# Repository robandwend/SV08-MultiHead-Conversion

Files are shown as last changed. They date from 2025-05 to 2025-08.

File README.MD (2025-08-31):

# SOVOL SV08 Multihead Conversion

I've converted my SV08 to a multi-toolhead printer. I'm keeping the costs way down by using the standard SV08 toolheads.

This repo contains the files designs I've used for mounting on the SV08.

NOTE: Files may change as I continue to develop this project - please refer to the commit's to see what's changed.

For full build overview on a SV08, I suggest watching Teaching Tech's series on doing the conversion. At this time he's not yet finished, and hasn't published any of the cad work - hence me re-inventing the wheel in this design. 
[video link](https://www.youtube.com/watch?v=G6kc_BnYU8w&t=2s)

For an initial intro here's a quick video I did to show the mount. 
[video link](https://www.youtube.com/watch?v=clDU7j5NY64)

## ModularDock

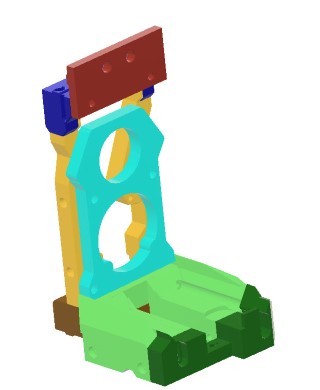
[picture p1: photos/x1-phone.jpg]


The head mount is based on using the modulardock From 
[here](https://github.com/DraftShift/ModularDock)

Specifically using these Components
- FrameShort
- 2020

The rear components for the SV08 modular dock can be found in the stl's folder.

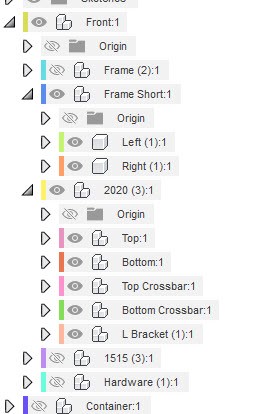
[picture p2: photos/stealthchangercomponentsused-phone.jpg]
Components


## *NEW* Modular dock - improved rest

I has now added a 2nd version of the dock components, implementing a better nozzle rest using a 5972k91 bearing (most common bearing used in many projects). This has been added to reduce nozzle 'dribble' whilst mounted. Two cut-down pen-springs are used to float the bearing.

The backplane stl is not needed with this version, as it's incorporated into the base itself.

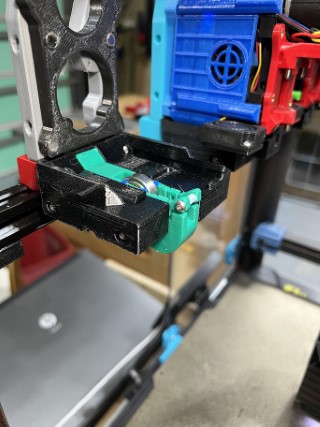
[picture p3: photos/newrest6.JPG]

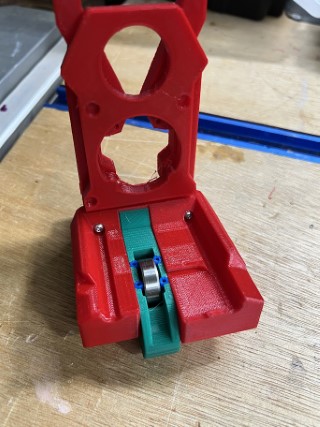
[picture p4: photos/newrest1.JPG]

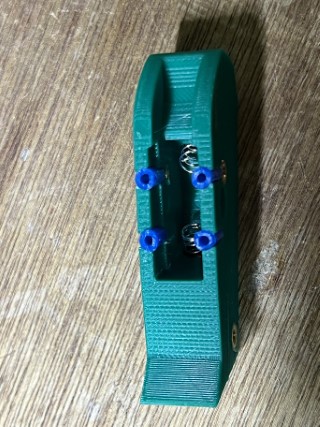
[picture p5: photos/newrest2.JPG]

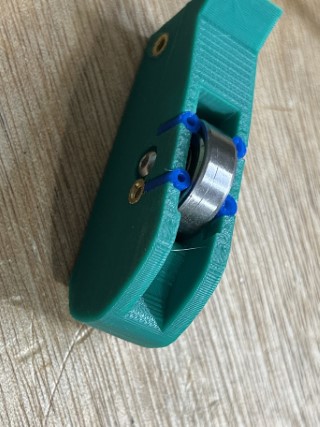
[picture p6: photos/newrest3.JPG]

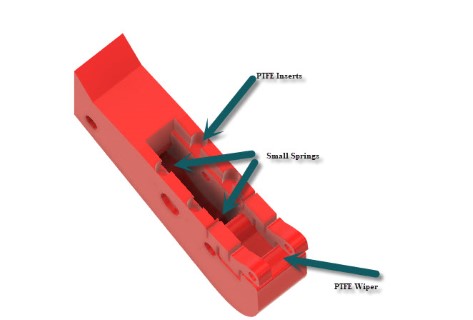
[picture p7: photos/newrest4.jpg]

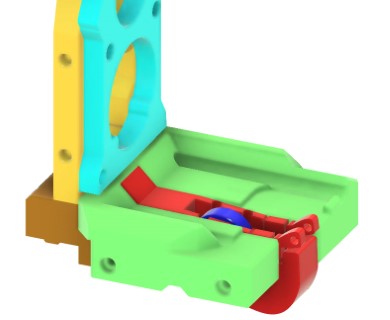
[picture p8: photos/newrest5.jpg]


## Stealthchanger 

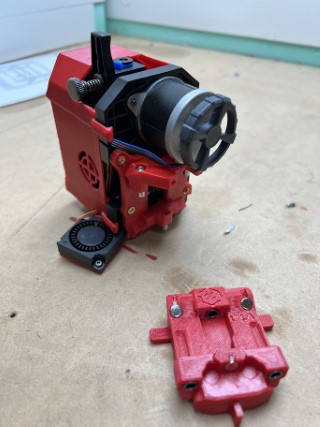
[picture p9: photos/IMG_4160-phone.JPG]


Follow the stealthchanger information found here - 
[link](https://github.com/DraftShift/StealthChanger)

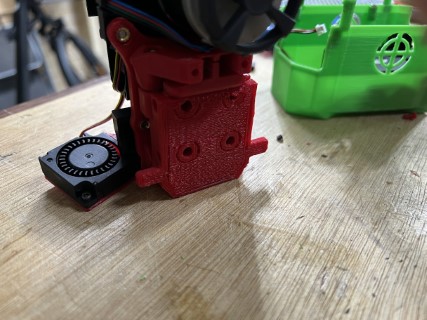
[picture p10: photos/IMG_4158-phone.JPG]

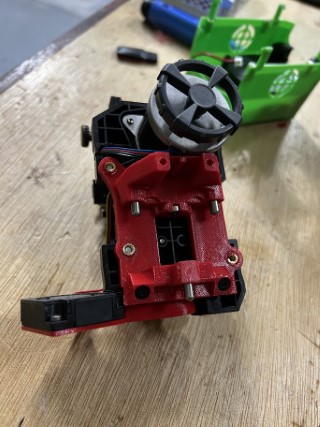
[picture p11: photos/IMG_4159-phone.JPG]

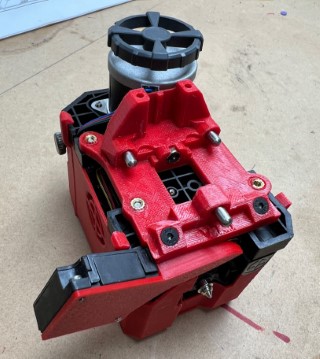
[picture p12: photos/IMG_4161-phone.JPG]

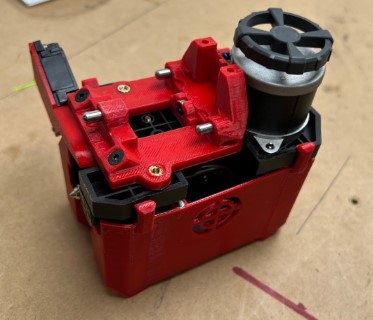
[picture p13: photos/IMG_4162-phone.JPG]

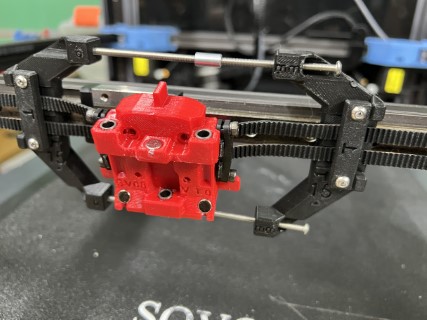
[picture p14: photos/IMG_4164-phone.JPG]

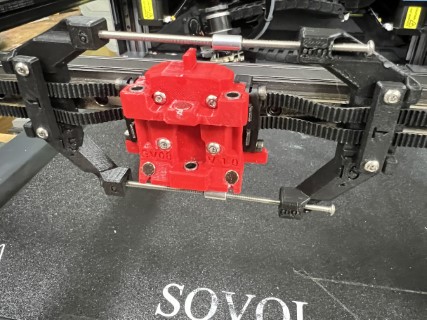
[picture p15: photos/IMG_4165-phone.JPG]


## Supports for docks

### Top 2020

The top 2020 extrusion has pre-built supports. Due to it's lenght and the small bolt holes, please ensure you compensate for any shrinkage when printing - size accuracy is key.

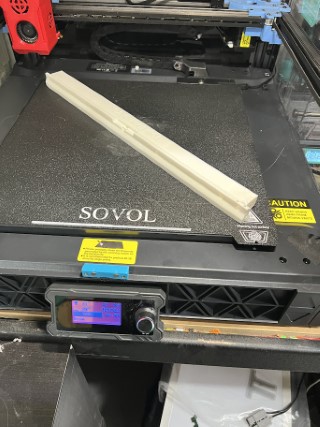
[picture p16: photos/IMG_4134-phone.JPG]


I've added a wave to the supports to try to assist with warping when printing in ABS/ASA

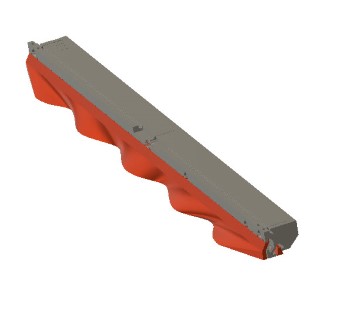
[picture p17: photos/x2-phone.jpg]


The print has supports built in, which will need snapping off after printing...

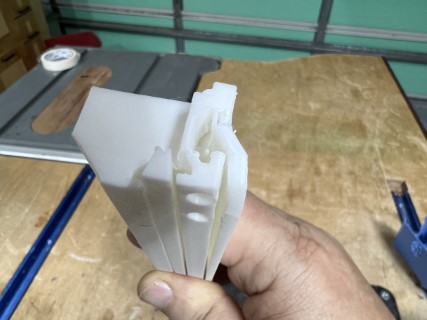
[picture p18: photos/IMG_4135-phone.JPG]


The light will need relocating (the screw holes can be used in attaching the 2020). I used some standard voron type tape to attach as shown.

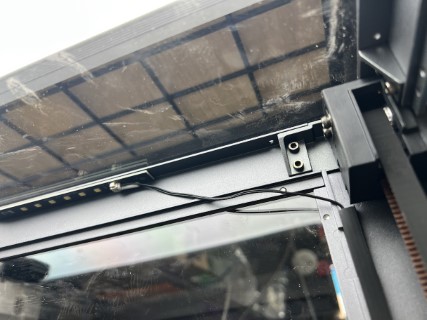
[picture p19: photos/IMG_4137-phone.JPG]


### Lower 2020

The bottom 2020 support pieces also have a hole printing guide. You MUST drill and tap, the bolt must NOT extend into the rear channel, since it would collide with the Z-Axis.

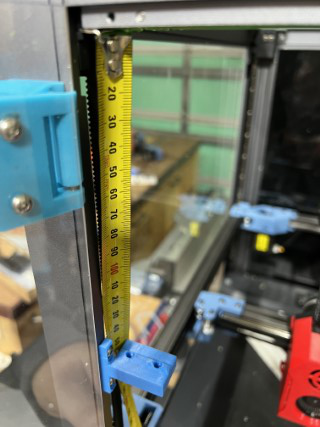
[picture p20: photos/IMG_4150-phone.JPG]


The head cover has built in supports for the clips, but may need manual supports on the front left/right indent area (depending on how well your bridging works.

Magnets - I've replaced the standard 4x3 magnets with 4x6 (or two 4x3) to increase pull strength.

## New power supply

I used this supply 
[supply link](https://www.amazon.com.au/dp/B0CN1JVD4Y?ref=ppx_yo2ov_dt_b_fed_asin_title&th=1)

And these mounts 
[mounts link](https://www.printables.com/model/1047201-sovol-sv08-power-supply-upgrade-mounting-parts)

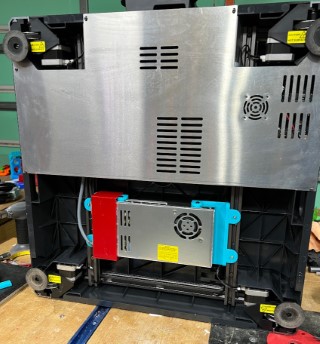
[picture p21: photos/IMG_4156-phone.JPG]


## Wiring General

I followed the method used by Teaching Tech 
[video link](https://youtu.be/OFGBXBn_xqs?t=1077)
using a birds-nest 
[birdsnest link](https://github.com/xbst/Birds-Nest)
 here's a handy clip from Teaching-Tech's video.
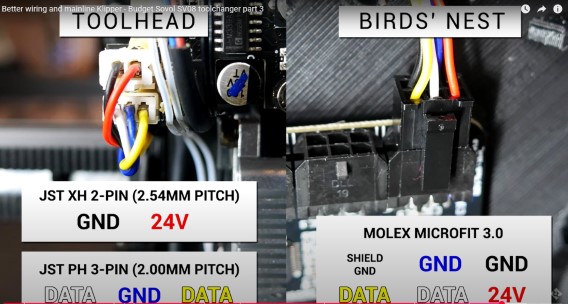
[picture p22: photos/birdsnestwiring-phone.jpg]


There's a simple birdnest attachment for the standard birdsnest fannypack_base that allows insertion of strain wires in the STL folder.
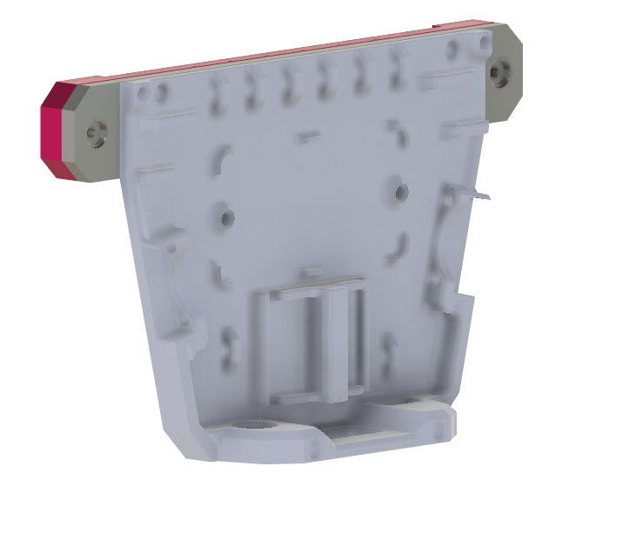
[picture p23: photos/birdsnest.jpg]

I bolted this to the rear of the SV08 - having drilled two small holes to bolt into.

## Rear fan

The rear fan is moved to allow undocking of the head. Simply removed the fan and replace the mount with the new one. 

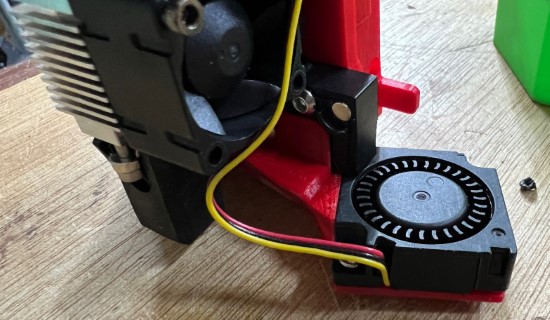
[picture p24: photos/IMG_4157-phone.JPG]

Components
Components
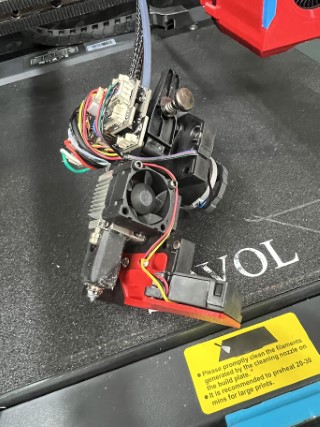
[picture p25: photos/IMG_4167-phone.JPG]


Note that this is fastened in the same holes, but from the front of the back plate rather than the back. 8mm M3 bolts will be needed.
To fasten the fan back on to the mount, either use the original bolts, or I have found using a 5mm M2.5 bolts gives a stronger fitting.

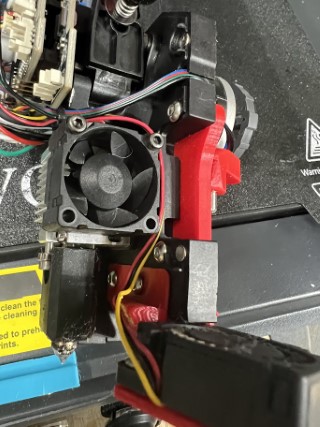
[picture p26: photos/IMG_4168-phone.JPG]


## Head cover

The design relies on this printed replacement head cover, which has additional rear clips, longer magnets, and 3 front magnets which attach to the dock. It also has additional cutouts to allow for the moved rear fan.

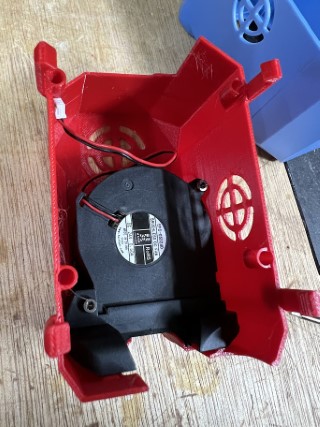
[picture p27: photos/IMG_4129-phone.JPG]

Components

## Umbilical mount point

To ensure the hotend umbilical could be adjusted to avoid collisions. This extension to the standard wire mount adds a small extension into which the strengthening wire could be mounted.

Note: A small recess should be made into the head-cover to fit this mount point. (I'll change the head-cover design at some point).

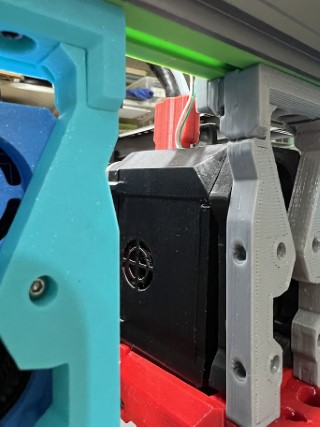
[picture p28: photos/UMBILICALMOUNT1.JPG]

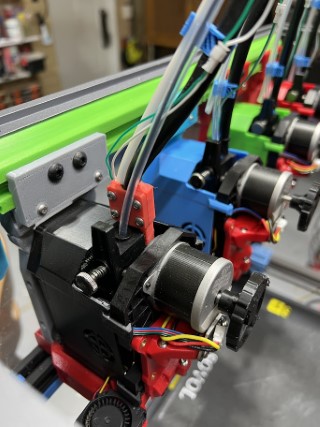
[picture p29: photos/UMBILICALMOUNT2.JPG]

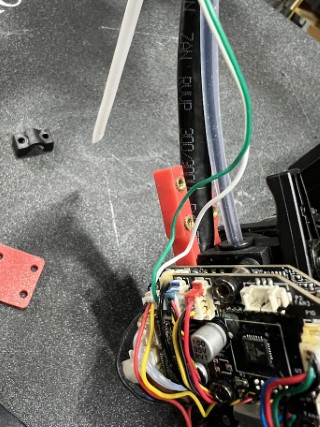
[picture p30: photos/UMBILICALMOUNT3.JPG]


## Bed Raise

The SV08 stealthchanger mount moves the head up 15mm and slightly forward. It will require raising.

The bed shims require M4 thread inserts.

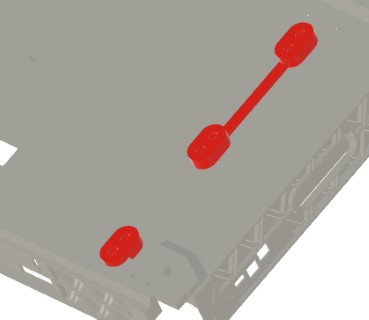
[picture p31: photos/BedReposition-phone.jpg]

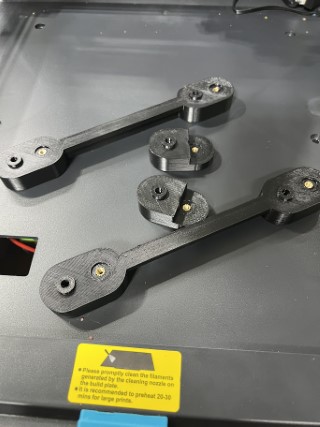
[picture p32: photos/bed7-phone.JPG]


Remove the bed, insert the shims as below (it may be a tight fit) use the 6 original bed screws to fasten the shims. Use 6 new M4 screws to fasten down the bed in it's new position.
Re-wire the bed.

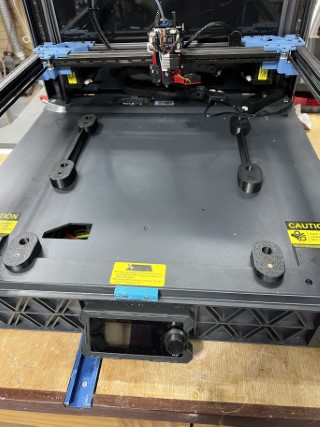
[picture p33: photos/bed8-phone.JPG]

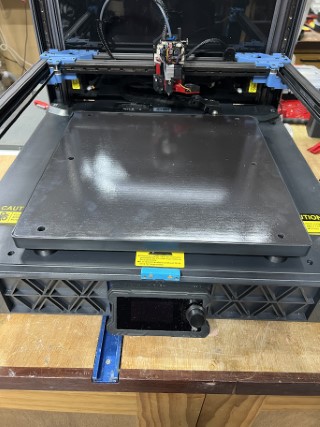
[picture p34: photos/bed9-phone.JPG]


## Sexball / SexBolt

To allow for automated x-y-z calibration between the heads [see this](https://github.com/viesturz/klipper-toolchanger/blob/main/tools_calibrate.md) I'm using a Sexball [sexball](https://github.com/DraftShift/StealthChanger/wiki/Bill-of-Materials#sexball-probe) which is based on the Sexbolt [sexbolt](https://mods.vorondesign.com/details/t1DBVlcUBbdEK6habEsVzg)

I reduced the height of the ball by 4mm to make it closer to the bed, by cutting the bar (with an angle grinder). This isn't required, but I felt it looked better.

NOTE: The use of the sexball requires the bed moving forward an extra 5mm - versions of the shim STL's are marked for this change.

This allows the tools_calibrate macro [macros](https://github.com/viesturz/klipper-toolchanger/blob/main/tools_calibrate.md) to be used to align all the heads.
	
### TOOL ALIGNMENT

I found these instructions to be the easiest way to align.
[tool alignment](https://github.com/viesturz/NozzleAlign) - to get the offsets of the tools from the sexball 

Here's the command sequence I ran:
> T0\
> SET_HEATER_TEMPERATURE HEATER=extruder TARGET=200\
> G28\
> CLEAN_NOZZLE\
> MOVE_OVER_PROBE\
> TOOL_LOCATE_SENSOR     # Sensor location at 281.150000,354.818750,1.853125\
> SET_HEATER_TEMPERATURE HEATER=extruder TARGET=0\

-- At this point I check the location with that defined in calibration-offsets.cfg, if they are off, then correct them and restart.

> SET_HEATER_TEMPERATURE HEATER=extruder1 TARGET=200\
> T1                     # Note my load/unload does an auto CLEAN-NOZZLE each time\
> MOVE_OVER_PROBE\
> TOOL_CALIBRATE_TOOL_OFFSET           # T1 = Tool offset is -0.662500,-0.031250,-0.290625\
> SET_HEATER_TEMPERATURE HEATER=extruder1 TARGET=0\

Repeat the above for T2,3,4

_T1 = Tool offset is -0.662500,-0.031250,-0.290625_\
_T2 = Tool offset is -0.750000,0.300000,0.163125_\
_T3 = Tool offset is -1.106250,-0.531250,-0.165000_\
	
Finally to ensure the belts haven't slipped (eg docking errors) I recheck location of T0...

> SET_HEATER_TEMPERATURE HEATER=extruder TARGET=200\
> T0\
> MOVE_OVER_PROBE\
> TOOL_CALIBRATE_TOOL_OFFSET\
> SET_HEATER_TEMPERATURE HEATER=extruder TARGET=0\

_Final T0 = _Tool offset is -0.000000,-0.006250,0.037500_  :-) Close enough :-)_

## TOPHAT

Based from Nadir's top hat [tophat](https://www.printables.com/model/865851-sovol-sv08-top-hat), I designed a tall version with clear panels and a magnetic rear access cover for the cabling.

Here you see the tophat with all it's parts colour seperated. 

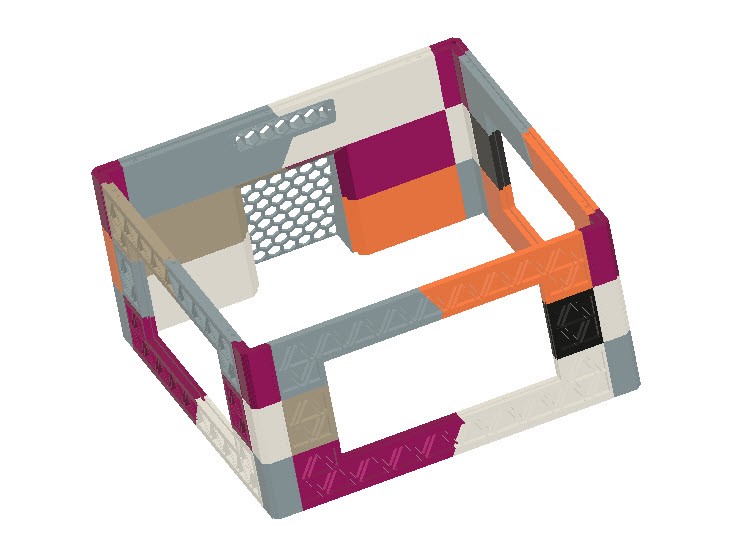
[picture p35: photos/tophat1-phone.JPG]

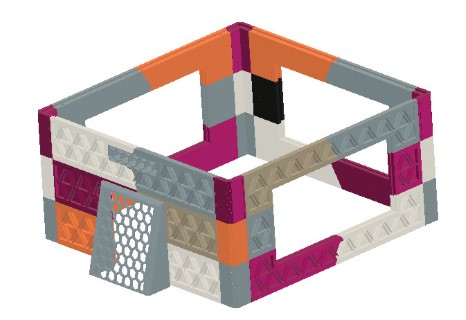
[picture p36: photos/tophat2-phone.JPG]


## RUNOUT DETECTOR

I've added a simple inline runout detector based on [this]https://www.printables.com/model/1084240-sovol-sv08-runout-sensor-on-head 
My version is here [my version]https://www.printables.com/model/1299711-generic-inline-runout-detector

Note it uses a 5.5mm ball (original used 5mm).

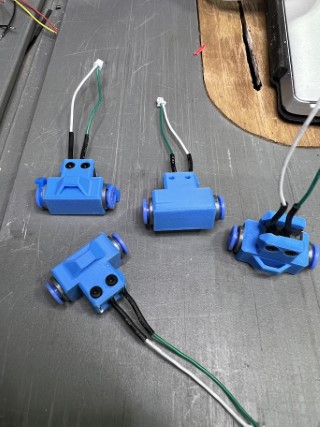
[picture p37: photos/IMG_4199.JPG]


Here you can see the wiring for the DETECTOR

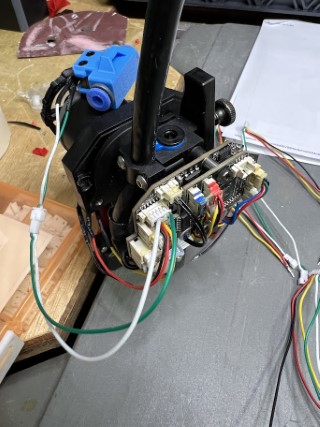
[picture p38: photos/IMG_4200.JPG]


## REAR ROCKER

Here's a simple rocker to allow the SV08 to be moved to it's back without squashing any cables at the rear.

The bottom part can use the original bolts since they appear to have plenty of spare length.

The top two bolts (holding in the panels) need replacing with 8mm m3's

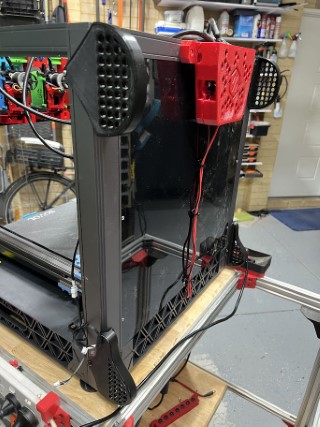
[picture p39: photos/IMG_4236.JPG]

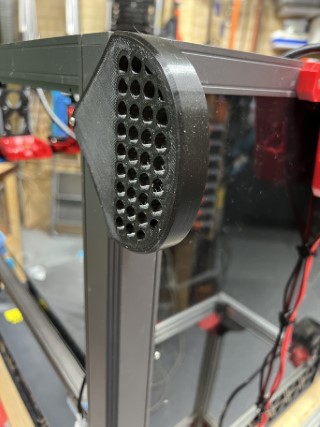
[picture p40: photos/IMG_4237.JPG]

Components

## BASE cover

Here's a simple cover to replace the stock metal one (still using the original fan) - I was not a fan of the original.

This will require a 36mm M3 bolt and an M3 2020 T-nut

Components

## Gantry Mounted wiper

I've created a modified version of [link] (https://www.printables.com/model/882364-new-version-adjustable-gantry-mounted-nozzle-seal) that has an extended and raised arm to fit this SV08 change. This can be seen in use in some of the videos.

## Final Klipper config files

My active klipper config files can all be found [here](https://github.com/robandwend/sv08-klipper)

# Over the top options...

As I've continued to tinker with this printer, I've made a few other modifications just for the fun of It

## Bambulab nozzle replacement.

I've used this converter to convert all nozzles to bambulabs. The original nozzles worked fine, but since all my other printers either use natively or have been converted to bambu nozzles, I thought I'd do this SV08 as well.

I've used both these converters
[link](https://www.printables.com/model/966176-remix-of-stephzics-sovol-sv08-bambu-lab-nozzle-ada)
[link](https://www.printables.com/model/944360-sovol-sv08-bambulab-clone-hotend-support)

Components
Components

## Extra camera processing

I've moved all camera processing (including new ones listed below) to an additional Raspberry PI 4B (I had it spare).
This is  running crowsnest to publish the cameras. The original klipper config for the camera's now points their IP's to this additional processor.

Components

A mount for this PI is in /stls/extras/

## Nozzle Cam

I've used this nozzle cam (only currently on head0)
[link](https://www.mintion.net/products/mintion-nozzle-camera?variant=48352784122166)

STL's for the head mount and electronics box are in /stls/extras/
nozzlecameramount

## Extra Camera's

In addition to the nozzle camera, I've added a camera to the rear top bar of the frame. 

This camera [link](https://www.aliexpress.com/item/1005005249688226.html)

Mount for the camera is in /stls/extras/

## Voice addition

Since I've now for the spare PI installed, I decided to add some speach to the printer.

I've added two small speakers (and a speaker pi-hat I had spare)...

The speakers were simply hot glued in place...

Components
Components
Components

Text to speach is achieved using pipper (see this video 
[link](https://www.youtube.com/watch?v=rjq5eZoWWSo_)
 - although the installation method has changed somewhat since the video was made.
 
 Here's the location of piper [link](https://github.com/OHF-Voice/piper1-gpl)
 
 In short, the install command is
 - pip install piper-tts  --break-system-packages
 
 (Test without the break-system-packages option first, to see if it's required on your installation).
 
 To get my audio amplifier working I had to do the following (thanks chatgpt)...

Edit /boot/config.txt and add the line:

   dtoverlay=audremap,pins_18_19

and reboot

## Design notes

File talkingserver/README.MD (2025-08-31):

# TALKING SERVER

Here's a simple way to add spoken audio to your klipper printer macros.

You'll need a raspberry pi to run the piper text-to-speech module. This could be your printers klipper CPU. This shouldn't affect the CPU load for printing, since usually you'll only need audio prompts when nothing is actually being printed (print starts, and error, print paused, load-more-filament, print-completed etc.).

## Add speakers

Either use the headphone jack of the PI or an audio tophat and some small speakers, and check audio works on the PI 

I've added two small speakers (and a speaker pi-hat I had spare)...

The speakers were simply hot glued in place...

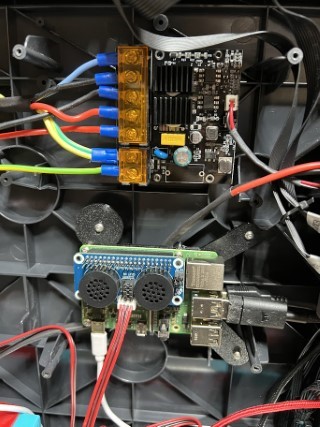
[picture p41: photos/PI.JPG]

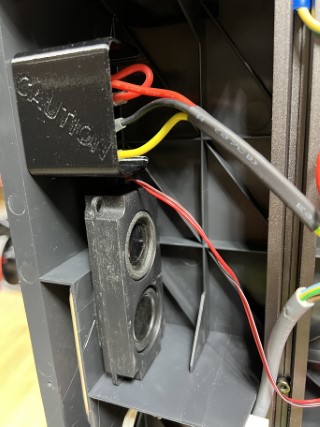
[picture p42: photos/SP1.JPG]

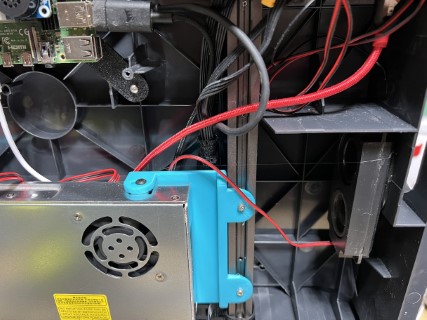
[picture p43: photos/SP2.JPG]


## Install piper 

Text to Speech is achieved using piper (see this video 
[link](https://www.youtube.com/watch?v=rjq5eZoWWSo_) )
 - although the installation method has changed somewhat since the video was made.
 
 Here's the location of piper [link](https://github.com/OHF-Voice/piper1-gpl)
 
 In short, the install command is
 ```
 pip install piper-tts  --break-system-packages
 ```
 
 (Test without the break-system-packages option first, to see if it's required on your installation).
 
 You can then add the speak dialect you'd like to use - using the instruction at 
 [link](https://github.com/OHF-Voice/piper1-gpl/blob/main/docs/CLI.md) - there's dozens of voices / languages to choose from.
 
 Here's an example of loading the Voice en_GB-southern_english_female-low
```
 python3 -m piper.download_voices en_GB-southern_english_female-low
```

 ### Audio pi hat
 
 To get my audio amplifier working I had to do the following (thanks chatgpt)...

Edit /boot/config.txt and add the line:
```
   dtoverlay=audremap,pins_18_19
```
and reboot

## Install this simple script

Copy the file ttserver.py from the talkingserver folder to your pi (I copied it into my home folder).

#### Change voice used in the script

If you choose to load a different voice (from en_GB-southern_english_female-low), then you will need to edit the ttserver.py file as follows

Edit ttserver.py and replace the language in line number 20 (for example to  en_GB-cori-high)

```
        "-m", "en_GB-southern_english_female-low",
```  

### Test the talkingserver

You can run the server manually to test by running this command from your PI:

- python3 ttsserver.py

This will start the server. You can then call the server from a web browser using a call of this format:

- http://ADDRESSOFYOURPI:4601/?text="Words%20to%20be%20spoken"

or from the PI itself using

```
curl "http://ADDRESSOFYOURPI:4601/?text=Hello%20world"
```

If you want the text to be repeated (unit the next time you call the server), add a ':' to the start of the text.

```
curl "http://ADDRESSOFYOURPI:4601/?text=This%20will%20repeat"
```

You can then pass an empty string (or anything else) to stop the text being spoken.

```
curl "http://ADDRESSOFYOURPI:4601/?text=%20"
```

You can also put any audio file on the server, and just get it to play it using a '>' in the text to indicat that this is a filename - thus...

```
curl "http://ADDRESSOFYOURPI:4601/?text=>filenametoplay.wav"
```

## Get the server to run as a service (on startup)

The most reliable way to make the script start on boot on a Raspberry Pi is to set it up as a systemd service.
That way, it will automatically run in the background after every reboot, and restart if it crashes.

Here’s how to do it:

```
sudo nano /etc/systemd/system/ttsserver.service
```

Paste this:
```
[Unit]
Description=Text-to-Speech Web Server
After=network.target

[Service]
ExecStart=/usr/bin/python3 /home/pi/ttsserver.py
WorkingDirectory=/home/pi
StandardOutput=inherit
StandardError=inherit
Restart=always
User=pi

[Install]
WantedBy=multi-user.target
```

Enable and start the service

```
sudo systemctl daemon-reload
sudo systemctl enable ttsserver.service
sudo systemctl start ttsserver.service
```

Check the status

```
sudo systemctl status tts_server.service
```

View logs if needed
```
journalctl -u ttsserver.service -f
```

## SAY - klipper macro to speak text.

Here's my gcode implementing the 'say'.

Paste this code into your config folder in a file called 'say.cfg', and ensure your printer.cfg includes this file.

```
[gcode_macro SAY]
description: Send text to remote TTS server

# --- CONFIGURABLE VARIABLES ---
variable_tts_host: "172.0.0.1"      # Change this to your TTS server IP/hostname
variable_tts_port: 4601             # Change this if you use a different port
# --------------------------------

gcode:
    {% set s = params.S|default("") %}
    {% if s == "" %}
        {action_respond_info("Usage: SAY S=\"your text here\"")}
    {% else %}
        {% set host = printer["gcode_macro SAY"].tts_host %}
        {% set port = printer["gcode_macro SAY"].tts_port %}
        {% set url  = "http://" ~ host ~ ":" ~ (port|string) %}
        {% set parms  = "--data-urlencode text=\'" ~ s ~ "\'" %}
        RUN_SHELL_COMMAND CMD="RUNSAY" PARAMS="{ parms } { url }"
    {% endif %}

[gcode_shell_command RUNSAY]
command: bash -c "curl -sG \"$0\" \"$1\" \"$2\""
timeout: 90.0
verbose: True

```

Now you can 'say' whatever you want from within your klipper macros...

### Speak a string

SAY S="PRINT HAS FINISHED"

### Repeat a string (2 second pause between each speech)

SAY S=">PAUSED - PLEASE LOAD FILAMENT"

### End a repeating speech

SAY S=" "   (Or any other SAY command)

### play a file

SAY S=">/home/sv08/FINISHED.wav"

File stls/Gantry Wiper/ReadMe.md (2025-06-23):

# Gantry Mounted Filament Wiper

This is based on this model [printables link](https://www.printables.com/model/882364-new-version-adjustable-gantry-mounted-nozzle-seal)

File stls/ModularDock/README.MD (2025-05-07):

# MODULAR DOCK

This folder contains the STLs that need adding to those from https://github.com/DraftShift/ModularDock

The mount is based on using the modulardock Front https://github.com/DraftShift/StealthChanger Specifically
- FrameShort
- 2020

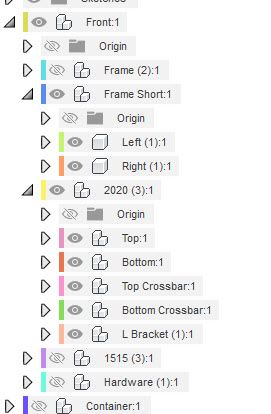
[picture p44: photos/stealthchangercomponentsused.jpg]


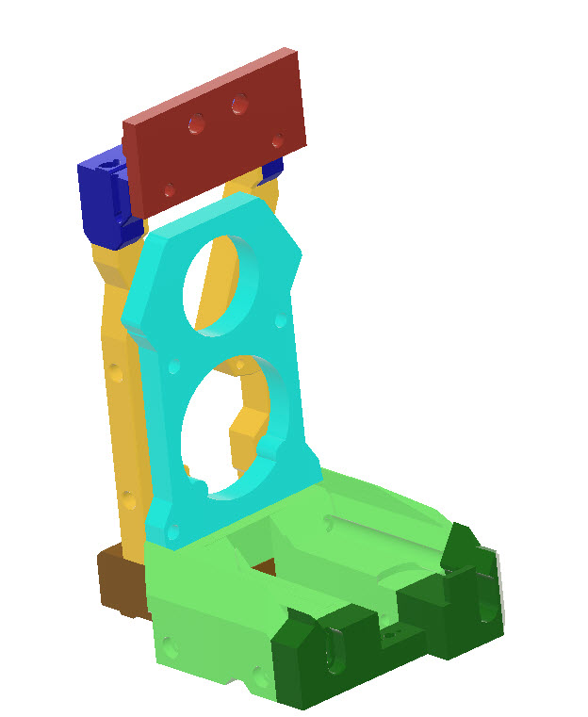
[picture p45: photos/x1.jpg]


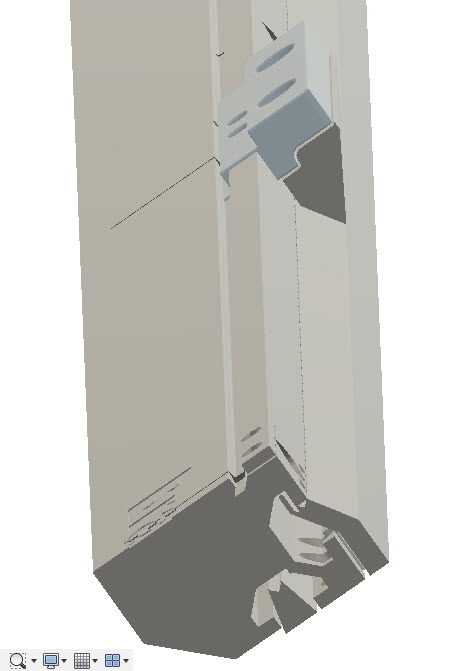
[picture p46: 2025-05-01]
photos/2020bar with door magnets.jpg

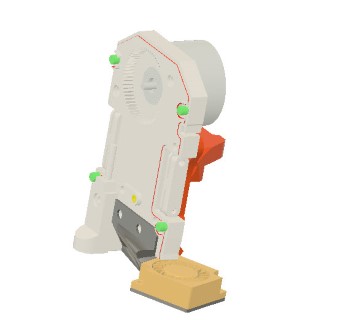
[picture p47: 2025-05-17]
photos/FanMount2-phone.jpg

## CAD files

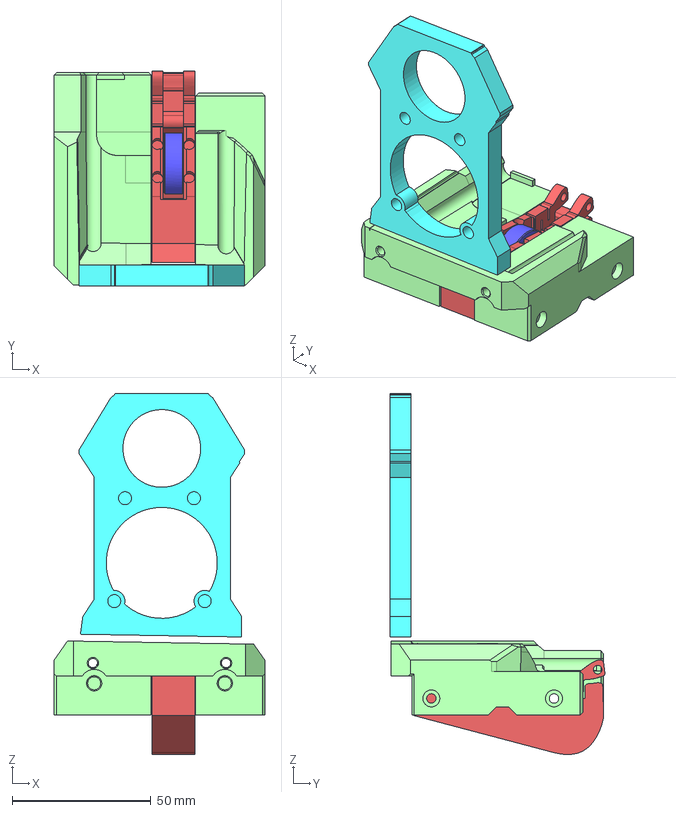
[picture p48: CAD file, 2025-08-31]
cads/Bearing Rest (New Bearing rest version).step
76.0 x 77.5 x 130.1 mm
Base (2) (1) (1)
FrontAttachmentPlate
PTFE Tube 15mm
M3 Threaded Insert (3)
M3x8 BHCS (3)
5972K91_Ball Bearing

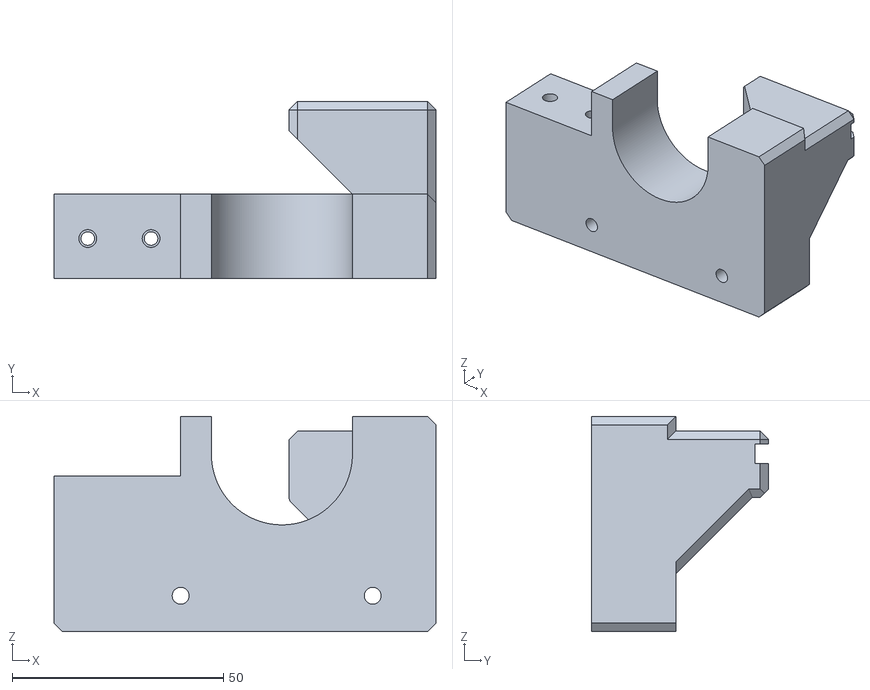
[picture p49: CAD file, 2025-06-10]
stls/BedRelocation/SexBallMount.stl
90.5 x 42.0 x 51.0

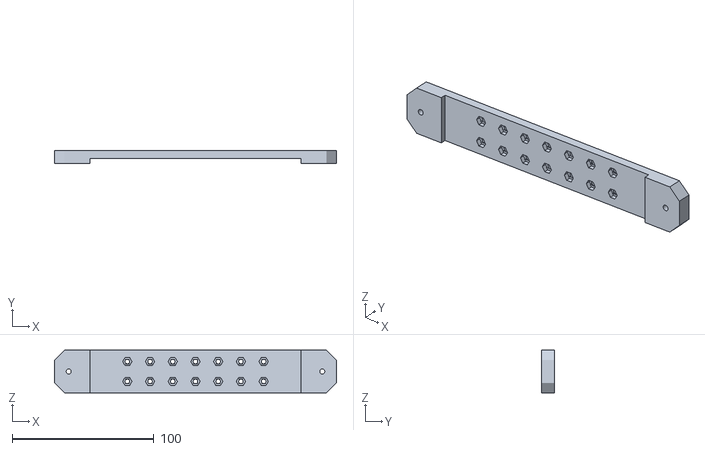
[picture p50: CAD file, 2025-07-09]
stls/Birdsnest/BirdsNestMount_BirdsNestMount v7_Back.stl
198.6 x 9.00 x 30.0

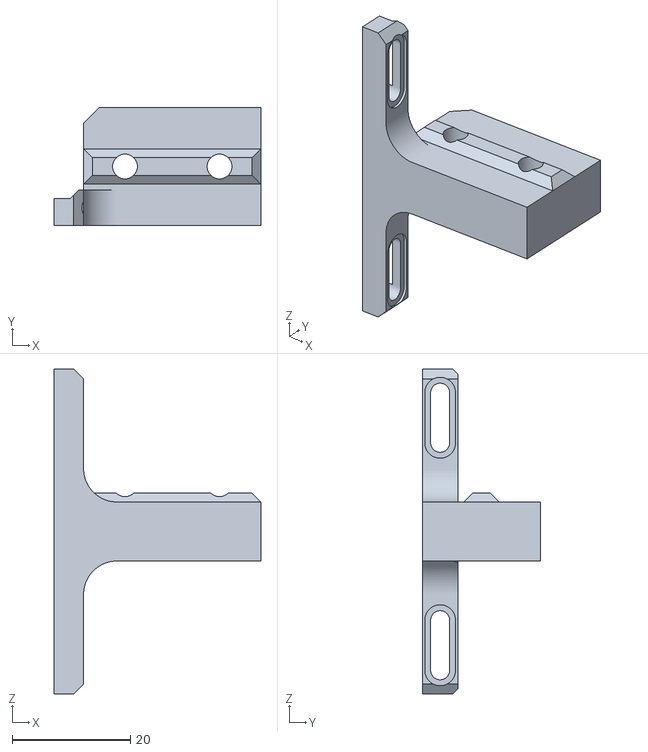
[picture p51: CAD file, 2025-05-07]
stls/Bottom2020MountingBar/SV08 Side 2020 mounts (v2).stl
35.0 x 20.0 x 55.0

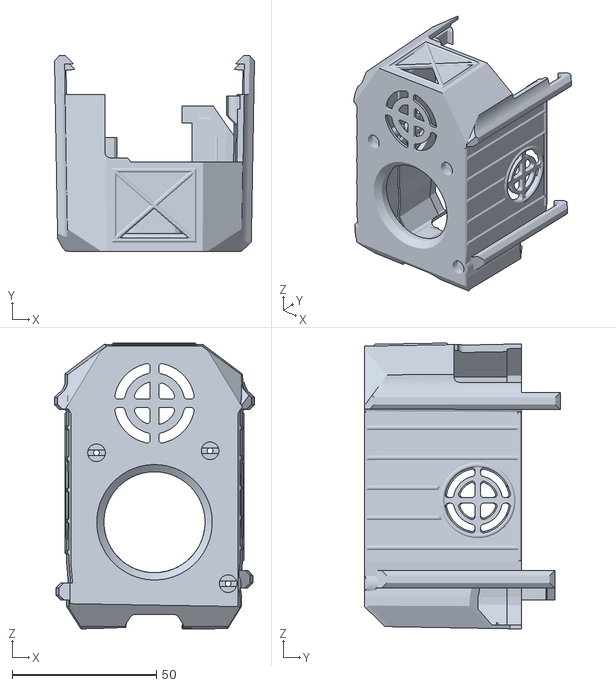
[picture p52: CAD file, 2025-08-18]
stls/Extruder Cover V3.stl
69.3 x 68.0 x 99.1

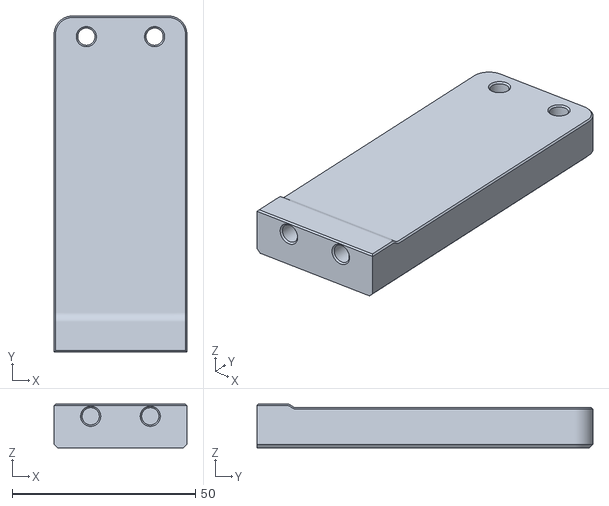
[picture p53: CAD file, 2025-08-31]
stls/Gantry Wiper/Brush mount (Extra sturdy).stl
36.3 x 91.7 x 12.0

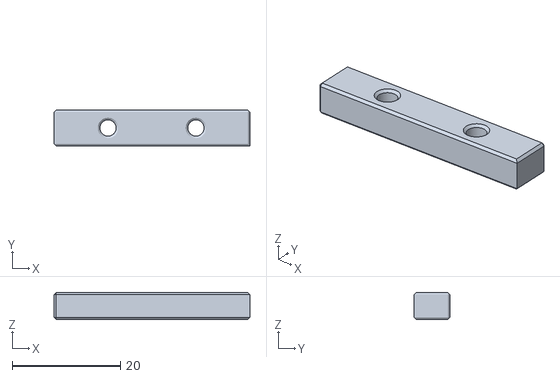
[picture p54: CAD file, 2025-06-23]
stls/Gantry Wiper/FilesPublishedInPrintables/brush-mount-extender-5mm.stl
36.3 x 6.70 x 5.00

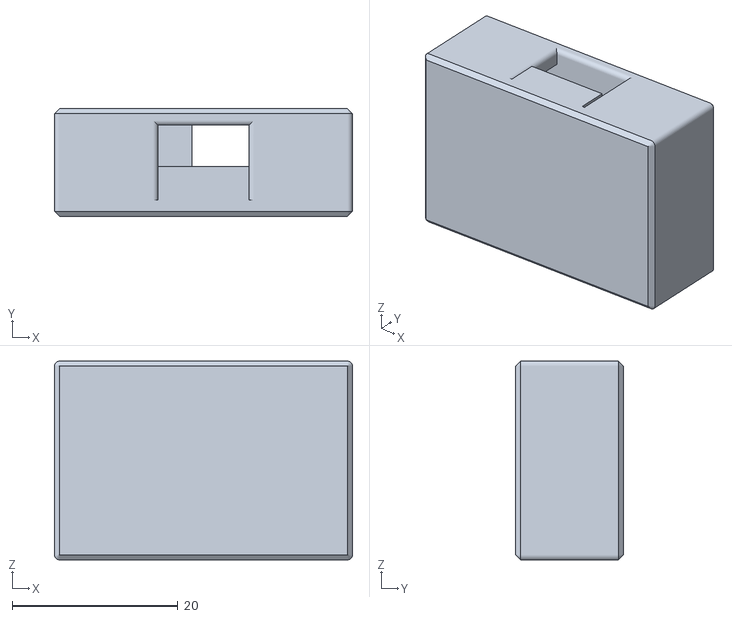
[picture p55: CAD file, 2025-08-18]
stls/Misc/Electronicsbox.stl
36.0 x 13.0 x 24.0

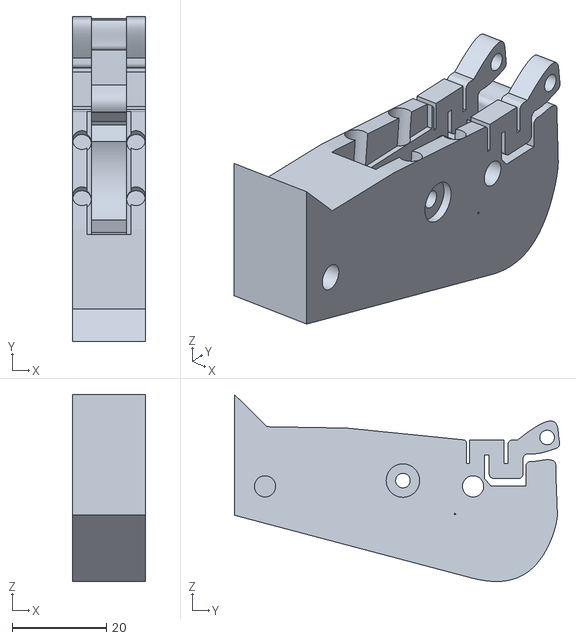
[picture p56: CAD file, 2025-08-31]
stls/ModularDock/BearingRest.stl
15.5 x 69.1 x 39.7

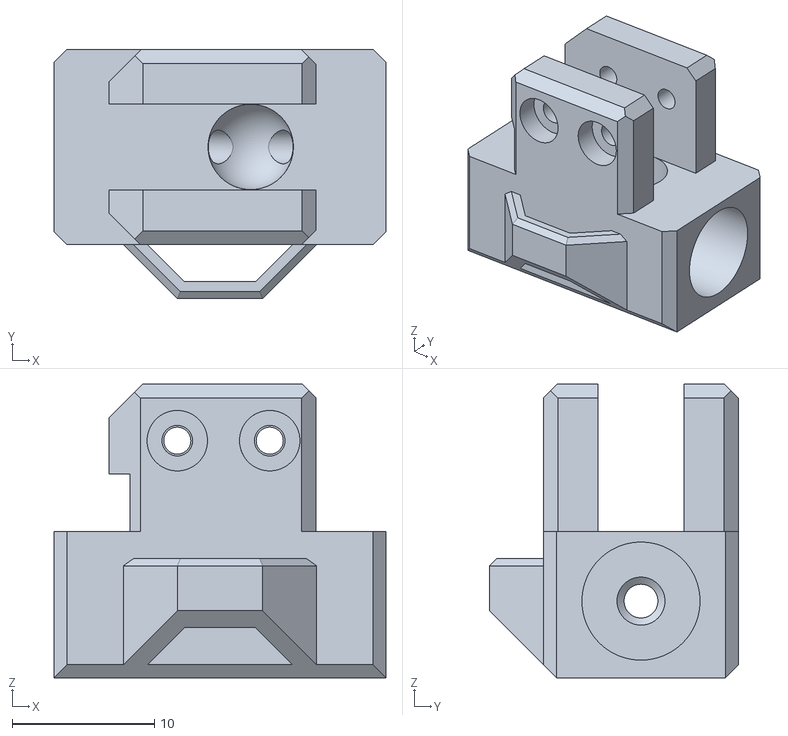
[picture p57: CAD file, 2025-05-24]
stls/Runout/Runout.stl
23.3 x 17.5 x 20.6

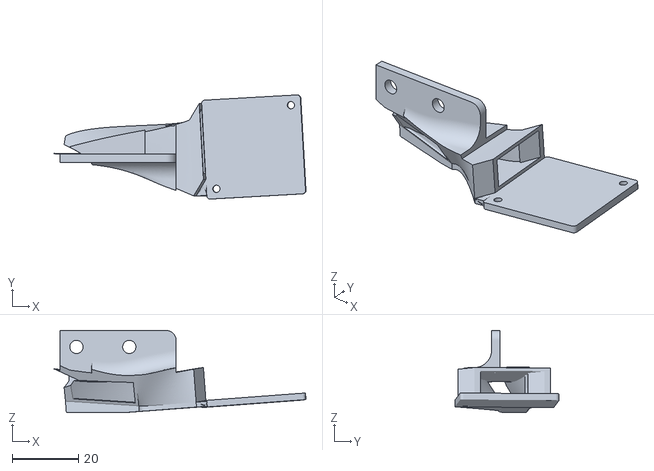
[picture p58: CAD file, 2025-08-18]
stls/StealthChanger/Fan Shroud.stl
76.3 x 31.5 x 24.9

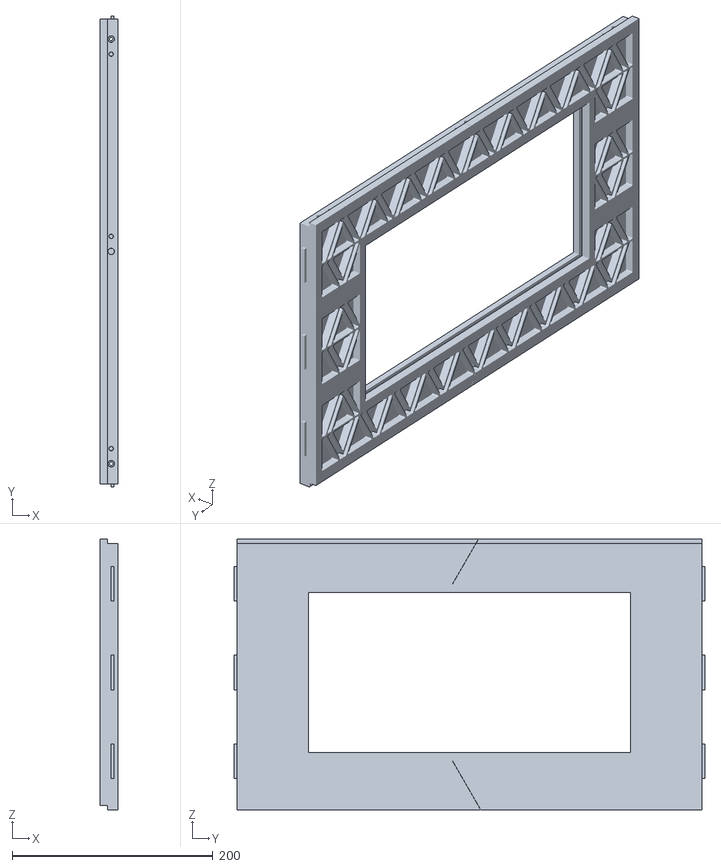
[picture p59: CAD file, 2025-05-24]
stls/TopHat/TopHat Left.stl
17.6 x 468.7 x 269.2

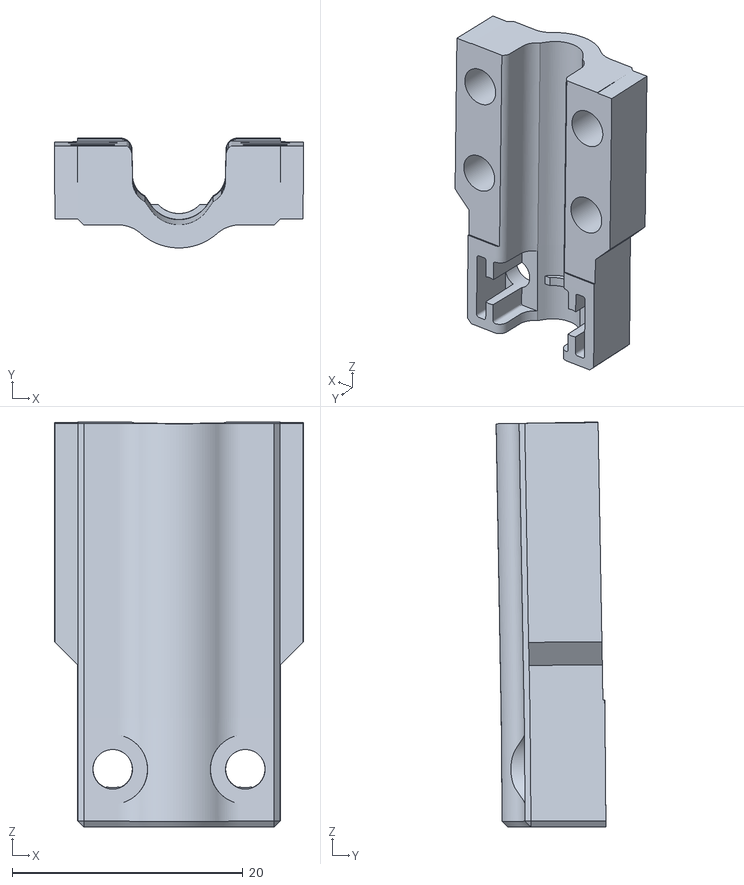
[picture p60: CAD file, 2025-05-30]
stls/UmbilicalMount/Wire clip with extension v3.stl_1.stl
21.6 x 9.53 x 35.1

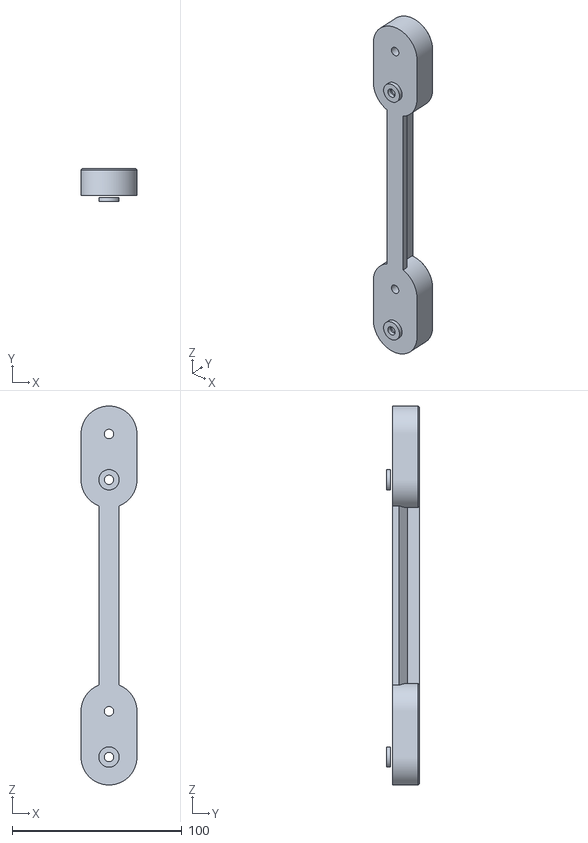
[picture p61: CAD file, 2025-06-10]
stls/BedRelocation/Bed Shim-Rear-Middle(For Sexball)-x2.stl
33.0 x 19.5 x 223.5

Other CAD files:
cads/Fan Shroud.stl
stls/Birdsnest/BirdsNestMount_BirdsNestMount v7_Front.stl
stls/Bottom2020MountingBar/Hole Drill Guide (v2).stl
stls/Gantry Wiper/Extrusion mount (Extra Sturdy).stl
cads/BedShims.step
cads/Extruder Cover v3.step
cads/Mount.step
cads/Runout.step
cads/SV08 Side 2020 mounts v3.step
cads/SV08 Side 2020 mounts v4.step
cads/SV08 Side 2020 mounts v5.step
cads/extruder cover.step
stls/BedRelocation/Bed Shim-Front(For Sexball)-x2.stl
stls/BedRelocation/Bed Shim-Front-x2.stl
stls/BedRelocation/Bed Shim-Rear-Middle-x2.stl
stls/BedRelocation/Shim for Bed v2.stl
stls/Bottom2020MountingBar/Hole Drill Guide.stl
stls/Bottom2020MountingBar/SV08 Side 2020 mounts.stl
stls/Extruder Cover.stl
stls/Gantry Wiper/Brush base SV08 Version.stl
stls/Gantry Wiper/Brush mount SV08 Version.stl
stls/Gantry Wiper/FilesPublishedInPrintables/brush-base.stl
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

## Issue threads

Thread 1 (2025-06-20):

SexBolt Options

caxtell, 2025-06-20:
I dont have an issue with your design so far, Ive been following your development and youre doing fantastic work. I wished to recommend to you Voron Nudge as an option instead of the sexbolt, Voron Nudge. Instead of just calibrating Z with your probe, the Nudge calibrates your X and Y of your nozzle as well as Z. Its highly recommended by other tool changing modders.

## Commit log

2025-05-01 V2 of lower 2020 supports
    [Hole Drill Guide (v2).stl, SV08 Side 2020 mounts (v2).stl, SV08 Side 2020 mounts v4.step]
2025-05-07 Latest update
    [Back.stl, Backplate.stl, Base.stl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]
2025-05-17 Top hat added
    [Back.stl, Bed Shim-Front-x2.stl, Bed Shim-Rear-Middle-x2.stl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]
2025-05-17 Bigger magnets for docking
    [Extruder Cover.stl]
2025-05-24 General tidyup
    [BotLeftLeft.stl, BotLeftRight.stl, Corners x 12.stl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]
2025-06-23 Working version
    [Brush base SV08 Version.stl, Brush mount SV08 Version.stl, brush-base.stl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]
2025-06-30 Fixed some STLS, side fan now at 90 deg. Nozzle pad moved 5mm and enlarged to better position
    [Fan Shroud.stl, ReplacementBackPlane(Pad Moved Left slightly).stl.stl, ReplacementBase(Pad Moved Left slightly).stl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]
2025-07-09 Birdsnest attachment added
    [BirdsNestMount_BirdsNestMount v7_Back.stl, BirdsNestMount_BirdsNestMount v7_Front.stl]
2025-08-18 Talking server added
    [Electronicsbox.stl, Extruder Cover V3.stl, Extruder Cover v3.step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]
2025-08-31 Added new bearing mount rest
    [Bearing Rest (New Bearing rest version).step, BearingRest.stl, Brush mount (Extra sturdy).stl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]
